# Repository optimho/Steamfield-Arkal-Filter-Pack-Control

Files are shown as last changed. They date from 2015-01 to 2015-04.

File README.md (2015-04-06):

# Steamfield-Arkal-Filter-Pack-Control

This controller was needed to supervise a filter pack that is installed in a remote location.
The filter pack will monitor the differential pressure over a series of filter packs, if the pressure gets too high the filter pack will 
initiate a series of back flushes. 

The filter pack is deficient in that, if it keeps flushing we need the filter to alarm and to open a bypass valve.

The filter controller was designed to monitor differential pressure input from a pressure sensor.
The controller also monitors the filter flush commands.

The firmware monitors for a high diff and filter run commands and alarms and bypasses the filter if required.

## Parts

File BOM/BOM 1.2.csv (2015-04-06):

RefDes | Value | Type | Pattern | RS Number
D1 |  | DBLS202G | DBS
D20 |  | 1N4007 | ES1GL Diode
D21 |  | LED | SML-31 LED
D23 |  | LED | SML-31 LED
HDR4_2 | 4 | TE connector 4 | 4 Way TE Connector | 452-612
HDR4_3 | 4 | TE connector 4 | 4 Way TE Connector | 452-612
HDR4_4 | 4 | TE connector 4 | 4 Way TE Connector | 452-612
HDR4_5 | 4 | TE connector 4 | 4 Way TE Connector | 452-612
J1 |  | HDR-1x8 | HDR-1x8
J2 |  | 1x2 Socket | CR0805
J3 |  | HDR-1x4 | HDR-1x4
J5 |  | 1x2 Socket | CR0805
J6 |  | 1x2 Socket | CR0805
J14 |  | 1x2 Socket | CR0805
K2.1 |  | G2R2 | G2R2 | 365-0529
K2.2 |  | G2R2 | G2R2
OPTOcoupler1 |  | CNY17F | CNY17F PDIP | 671-2699
OPTOcoupler2 |  | CNY17F | CNY17F PDIP | 671-2699
OPTOcoupler3 |  | CNY17F | CNY17F PDIP | 671-2699
OPTOcoupler4 |  | CNY17F | CNY17F PDIP | 671-2699
Q3 |  | BC639 | BCY-3/D5.2 | 800-9585
R1 | 10K | RES_0805 | RES_0805 | 788-3972
R19 | 2.2 micro henry | IND_0805 | IND_0805
R22 | 1k | RES_0805 | RES_0805 | 223-0427
R24 | 1k | RES_0805 | RES_0805 | 740-8971
R25 | 1k | RES_0805 | RES_0805 | 740-8971
R26 | 4700 ohm | RES_0805 | RES_0805 | 740-9031
R27 | 4700 ohm | RES_0805 | RES_0805 | 740-9031
R28 | 1k ohm | RES_0805 | RES_0805 | 740-8971
R29 | 1k ohm | RES_0805 | RES_0805 | 740-8971
R30 | 10k ohm | RES_0805 | RES_0805 | 788-3972
R31 | 10k ohm | RES_0805 | RES_0805 | 788-3972
R32 | 4700 ohm | RES_0805 | RES_0805 | 740-9031
R33 | 1k ohm | RES_0805 | RES_0805 | 740-8971
R34 | 1k ohm | RES_0805 | RES_0805 | 740-8971
R35 | 1k ohm | RES_0805 | RES_0805 | 788-3972
R36 | 10k ohm | RES_0805 | RES_0805 | 788-3972
R37 | 10k ohm | RES_0805 | RES_0805 | 788-3972
R42 | 1k ohm | RES_0805 | RES_0805 | 740-8971
R43 | 1k ohm | RES_0805 | RES_0805 | 740-8971
R44 | 1k ohm | RES_0805 | RES_0805 | 740-8971
R45 | 1k ohm | RES_0805 | RES_0805 | 740-8971
R48 | 2.0k | RES_2512 | RES_2512
R55 | 1k | RES_0805 | RES_0805 | 740-8971
R60 | 1K | RES_0805 | RES_0805 | 788-3972
R69 | 1k | RES_0805 | RES_0805 | 740-8971
R70 | 1K | RES_0805 | RES_0805 | 740-3971

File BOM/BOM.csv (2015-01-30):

RefDes | Value | Type | Pattern | RS Number | RS Number | Parallax_PN
C1 | 10 uF | CAP_1210 | T491 series size C |  |  | 210-10001
C3 | 10 uF | CAP_1210 | T491 series size C |  |  | 210-10001
C4 | 10 uF | CAP_1210 | T491 series size C |  |  | 210-10001
C5 | 1 uF | CAP_1210 | T491 series size A |  |  | 210-10001
C17 | 10 u farad | CAP | Aluminium Cap 8 x 6.2 | 490-8267 | 490-8267
C18 | 10 uf | CAP100RP | Aluminium Cap 8 x 6.2
C23 | 10u farad | CAP | T491 series size D
C24 | 3.3 u farad | CAP | Aluminium Cap 8 x 6.2
C25 | 3.3 uf | CAP_1206 | Aluminium Cap 8 x 6.2
D15 |  | 1N4002 | ES1GL Diode
D16 |  | DIODE_1206 | ES1GL Diode | 796-5800P | 796-5800P
D17 |  | DIODE_1206 | ES1GL Diode | 796-5800P | 796-5800P
D18 |  | DIODE_1206 | ES1GL Diode | 796-5800P | 796-5800P
D19 |  | DIODE_1206 | ES1GL Diode | 796-5800P | 796-5800P
D20 |  | 1N4007 | ES1GL Diode
D21 |  | LED | SML-31 LED
D22 |  | LED | SML-31 LED
D23 |  | LED | SML-31 LED
HDR4_1 | 4 | Header 4 | HDR-1X4 | 452-612 | 452-612
HDR4_2 | 4 | TE connector 4 | 4 Way TE Connector | 452-612 | 452-612
HDR4_3 | 4 | TE connector 4 | 4 Way TE Connector | 452-612 | 452-612
HDR4_4 | 4 | TE connector 4 | 4 Way TE Connector | 452-612 | 452-612
HDR4_5 | 4 | TE connector 4 | 4 Way TE Connector | 452-612 | 452-612
J1 |  | 1x2 Socket | CR0805 |  |  | n/a
J2 |  | 1x2 Socket | CR0805 |  |  | n/a
J12 |  | 1x2 Socket | CR0805 |  |  | n/a
J14 |  | 1x2 Socket | CR0805 |  |  | n/a
K1 |  | SWITCH8DIP | Dip Switch
K2.1 |  | G2R2 | G2R2 | 365-0529 | 365-0529
K2.2 |  | G2R2 | G2R2
OPTOcoupler1 |  | CNY17F | CNY17F PDIP | 671-2699 | 671-2699
OPTOcoupler2 |  | CNY17F | CNY17F PDIP | 671-2699 | 671-2699
OPTOcoupler3 |  | CNY17F | CNY17F PDIP | 671-2699 | 671-2699
OPTOcoupler4 |  | CNY17F | CNY17F PDIP | 671-2699 | 671-2699
Q3 |  | BC639 | BCY-3/D5.2 | 800-9585 | 800-9585
R1 |  | RES_0805 | RES_0805 | 788-3972 | 788-3972
R2 |  | RES_0805 | RES_0805 | 788-3972 | 788-3972
R19 | 2.2 micro henry | IND_0805 | IND_0805
R21 | 1K | RES_0805 | RES_0805 | 788-3972 | 788-3972
R22 | 1k | RES_0805 | RES_0805 | 223-0427 | 223-0427
R24 | 1k | RES_0805 | RES_0805 | 740-8971 | 740-8971
R25 | 1k | RES_0805 | RES_0805 | 740-8971 | 740-8971
R26 | 4700 ohm | RES_0805 | RES_0805 | 740-9031 | 740-9031
R27 | 4700 ohm | RES_0805 | RES_0805 | 740-9031 | 740-9031
R28 | 1k ohm | RES_0805 | RES_0805 | 740-8971 | 740-8971
R29 | 1k ohm | RES_0805 | RES_0805 | 740-8971 | 740-8971
R30 | 10k ohm | RES_0805 | RES_0805 | 788-3972 | 788-3972
R31 | 10k ohm | RES_0805 | RES_0805 | 788-3972 | 788-3972
R32 | 4700 ohm | RES_0805 | RES_0805 | 740-9031 | 740-9031
R33 | 1k ohm | RES_0805 | RES_0805 | 740-8971 | 740-8971
R34 | 1k ohm | RES_0805 | RES_0805 | 740-8971 | 740-8971
R35 | 1k ohm | RES_0805 | RES_0805 | 788-3972 | 788-3972
R36 | 10k ohm | RES_0805 | RES_0805 | 788-3972 | 788-3972
R37 | 10k ohm | RES_0805 | RES_0805 | 788-3972 | 788-3972
R38 | 10k ohm | RES_0805 | RES_0805 | 788-3972 | 788-3972
R42 | 1k ohm | RES_0805 | RES_0805 | 740-8971 | 740-8971
R43 | 1k ohm | RES_0805 | RES_0805 | 740-8971 | 740-8971
R44 | 1k ohm | RES_0805 | RES_0805 | 740-8971 | 740-8971
R45 | 1k ohm | RES_0805 | RES_0805 | 740-8971 | 740-8971
R46 | 220 ohm | RES_0805 | SMA | 721-6889P | 721-6889P
R47 | 666 ohm | RES_0805 | RES_0805 | 708-6070 | 708-6070
R48 | 2.0k | RES_2512 | RES_2512
R49 | 1k | RES_0805 | RES_1206 | 740-3971 | 740-3971
R50 | 1K | RES_0805 | RES_1206 | 740-3971 | 740-3971
R51 | 1K | RES_0805 | RES_1206 | 740-3971 | 740-3971
R52 | 1K | RES_0805 | RES_1206 | 740-3971 | 740-3971
R53 | 1K | RES_0805 | RES_1206 | 740-3971 | 740-3971
R54 | 1K | RES_0805 | RES_0805 | 740-8971 | 740-8971
R55 | 1k | RES_0805 | RES_0805 | 740-8971 | 740-8971
R56 | 1K | RES_0805 | RES_1206 | 740-3971 | 740-3971
R57 | 1K | RES_0805 | RES_1206 | 740-3971 | 740-3971
R58 | 1K | RES_0805 | RES_1206 | 740-3971 | 740-3971
R59 | 10K | RES_0805 | RES_0805 | 788-3972 | 788-3972
R60 | 1K | RES_0805 | RES_0805 | 788-3972 | 788-3972
R61 | 10K | RES_0805 | RES_0805 | 788-3972 | 788-3972
R62 | 10K | RES_0805 | RES_0805 | 788-3972 | 788-3972
R63 | 10K | RES_0805 | RES_0805 | 788-3972 | 788-3972
R64 | 10K | RES_0805 | RES_0805 | 788-3972 | 788-3972
R65 | 10K | RES_0805 | RES_0805 | 788-3972 | 788-3972
R66 | 10K | RES_0805 | RES_0805 | 788-3972 | 788-3972
R67 | 10K | RES_0805 | RES_0805 | 788-3972 | 788-3972
R69 | 1k | RES_0805 | RES_0805 | 740-8971 | 740-8971
R70 | 1K | RES_0805 | RES_0805 | 740-3971 | 740-3971
S1 |  | Pushbutton | Tactile Switch | 793-1642 | 793-1642 | 400-10003
U1 |  | P8X32A-Q44 | LQFP_44/10x10x0.8 | 450-626p | 450-626p
U2 |  | 24LC256MS | TSOP-8/3x6 | 738-0069 | 738-0069
U3 |  | LM1086IS-3.3 | TO263-4/14x10.2x2.54 | 533-9426P | 533-9426P
U9 |  | LM338T | SFM-3/W10.7 | 640-7839 | 640-7839
X1 |  | CRYSTALHC49U-V | HC49U-V | 814-9396P | 814-9396P

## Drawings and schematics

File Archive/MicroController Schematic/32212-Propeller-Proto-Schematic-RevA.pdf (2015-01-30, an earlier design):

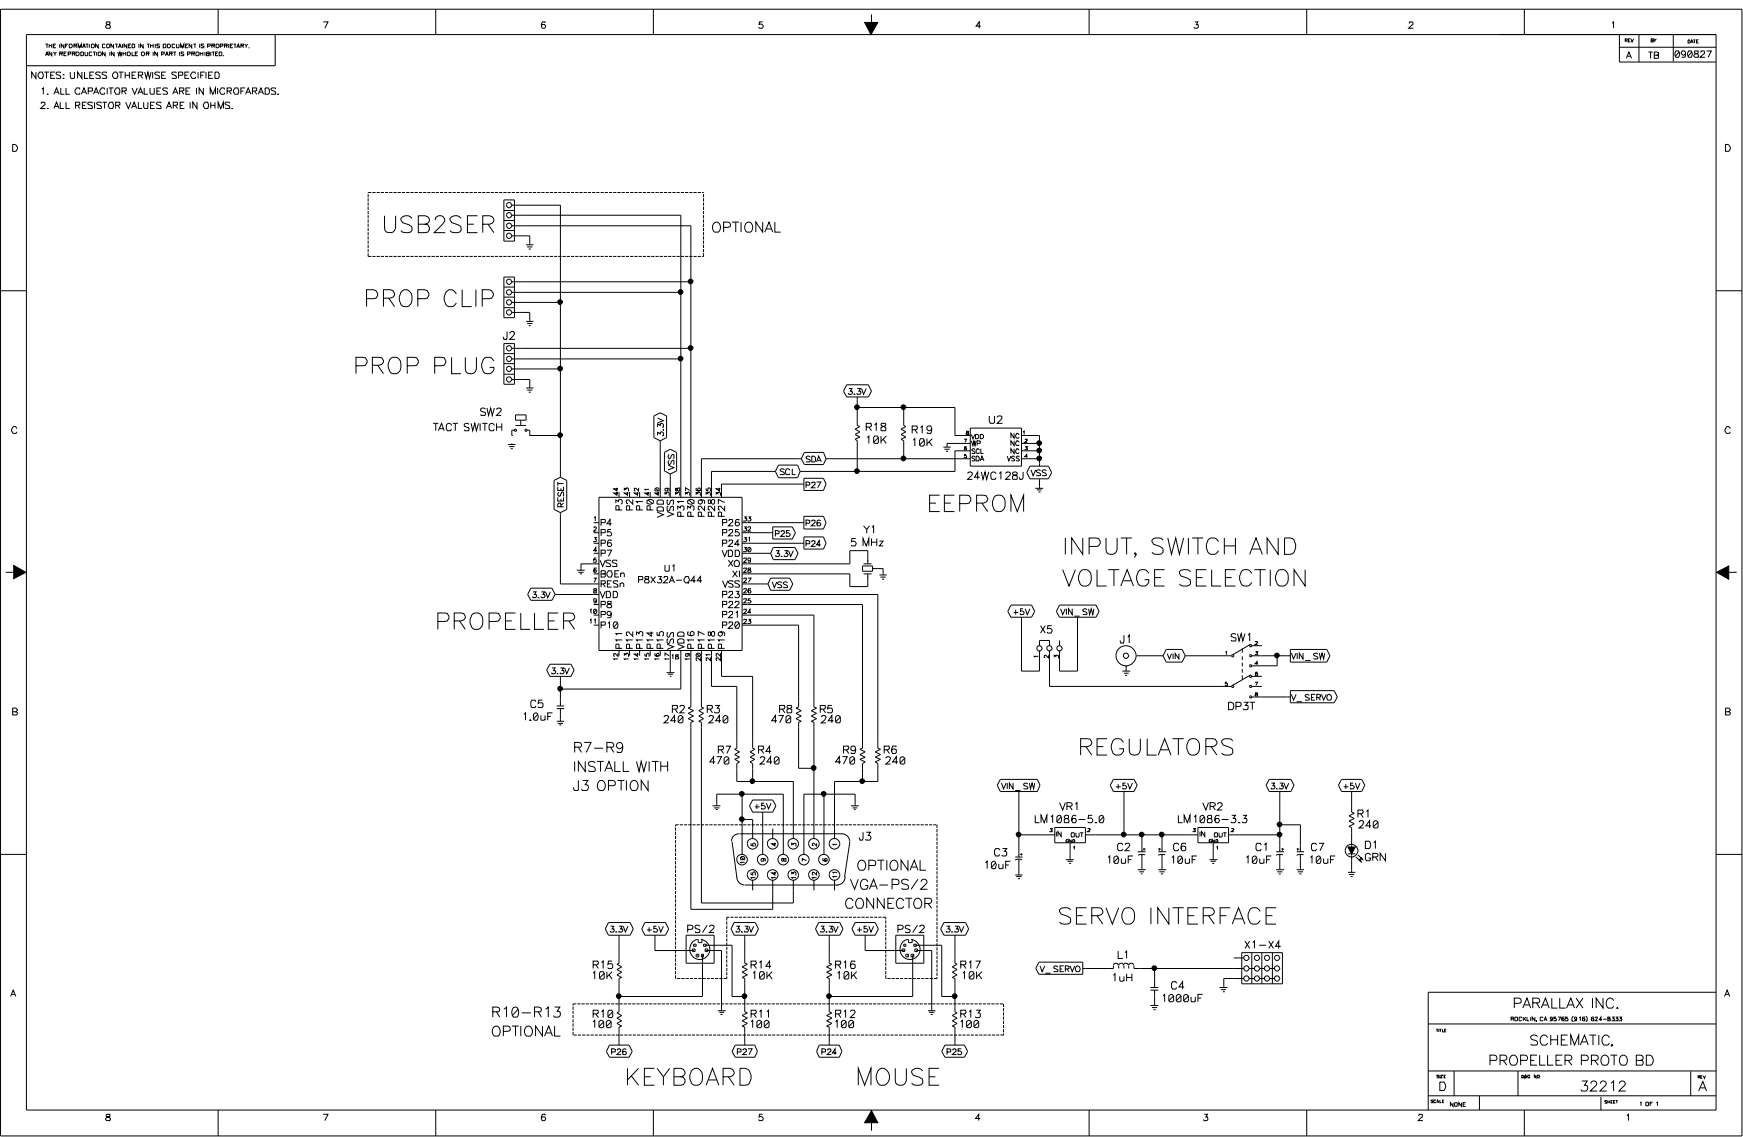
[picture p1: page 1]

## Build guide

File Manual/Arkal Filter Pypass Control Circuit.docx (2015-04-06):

Arkal Filter Control

Contact Energy

Filter Control Board

https://github.com/optimho/Steamfield-Arkal-Filter-Pack-Control

###### Table of Contents

###### Operation

t

He Filter control module monitors the differential pressure across the filter Pack and also counts the amount of filter flush cycles. If the filter pack is constantly flushing and not able to clear the high differential, then the bypass will be opened and an alarm will be raised.

Refer to the Arkal filter documentation to maintain a blockage in the filter.

All documentation for the project is available on Github, follow the following URL

https://github.com/optimho/Steamfield-Arkal-Filter-Pack-Control

###### Control

The reset button will be illuminated on the front of the panel if the filter control has operated the bypass valve. To resume normal operation reset the filter control by pressing the illuminated button. The light should extinguish and the bypass valve should close, if the DP (Differential Pressure) has returned to normal.

###### Settings

The board was originally designed with dipswitches, but the dipswitch was resigned and the firmware was added to the project. All changes and customization can be done directly in the firmware.

If you want to modify or monitor the controller install the Simple IDE software that is available at the Github address above under the firmware folder.

# Connection Diagram

###### Maintenance

There is no maintenance required apart from testing and inspecting the operation of the controller at regular intervals.

###### Schematics

###### Firmware Listing

/*

*

*SteamFileldController.c

*

*Main listing

Steamfield Controller Firmware

controls the bypass valve, opens if the flush cycles are to numerous.

functions recordEvent( period) this function will return the amount of operations preformed in a specified period in seconds

The function is a low speed function and cannot really handle inputs at a frequency less than 1 second.

*/

#include <TimeFile.h>

#define period 90 // This is the period that the amount of flush starts are counted

#define diffAlarm 10 // This is the period that initiates a diff Alarm

#define flushValve 26 //

#define highDiff 1 //

#define filter1 2 //define the micro processor pin usage

#define filter2 3 //

#define filter3 4 //

#define clear 5 // Reset input

#define FilterStarts 5

char *timeOfEvent;

int i=0;

int placeHolder1=0;

int placeHolder2=0;

int placeHolder3=0;

int diffState=0; // Time differential pressure became high

int diffTime=0;

int currentTime=0; // The amount of seconds since the last time reset or switch on

int amountOfEvents=0; // amount of flush operations recorded in a specified period

int main()

{

print("********************************* \n");

print("********************************* \n");

print("******* Steamfield *****\n");

print("**** Arkal filter controller ***\n");

print("**** Contact Energy **** \n");

print("********************************* \n");

print("****** Michael *** \n");

print("****** Rick *** \n");

print("****** Grant *** \n");

print("********************************* \n");

print("**** 15-03-2015 version 1.0 ** \n");

print("********************************* \n");

print(" \n");

print(" \n");

pause(1000);

for(;;)

{

int diff = input(highDiff);

int flush_1 = input(filter1);

int flush_1_old;

int flush_2 = input(filter2);

int flush_2_old;

int flush_3 = input(filter3);

int flush_3_old;

int clr = input(clear);

currentTime=timeNow(); // the time now is currentTime

/* This section is to determine if a flush cycle has been completed.

* ************************************************************************/

if (placeHolder2 != sequenceCheck(flush_1, flush_2, flush_3))

{

//print(" Flush sequence complete %d \n", sequenceCheck(flush_1, flush_2, flush_3));

}

placeHolder2=sequenceCheck(flush_1, flush_2, flush_3);

/* Prints to terminal some program information

* ************************************************************************/

if (placeHolder1 != indexer())

{

print("number of filter starts %d per %d seconds - filter %d %d %d \n", indexer(), period, flush_1, flush_2 ,flush_3);

}

placeHolder1=indexer();

//printf("amount of triggers per period %i \n", amountOfEvents);

// printf("Seconds since last reset %i \n",currentTime);

// print("diff Pressure = %d\n", diff);

// print("flush 1 = %d\n", flush_1);

// print("flush 2 = %d\n", flush_2);

// print("flush 3 = %d\n", flush_3);

// print("Diff High since = %d \n", diffState);

// print("************************ \n");

//print(" \n");

/* This section is to determine if a flush has been initiated.

* ************************************************************************/

if ((flush_1 > flush_1_old) || (flush_2 > flush_2_old) || (flush_3 > flush_3_old))

{

amountOfEvents=recordEvent();

}

flush_1_old=flush_1;

flush_2_old=flush_2;

flush_3_old=flush_3;

/* This section is to determine how long the high diff alarm has been active.

* ************************************************************************/

if ((diff==1) && (diffState==0)) //If there is a high diff and there is not currently a high diff already then save the time

{

diffState = currentTime;

//diffTime = diffState; // That the diff went high

}

else if ((diff==1) && (diffState>0)) //If there is a high diff and there is not currently a high diff already then save the time

{

diffTime = currentTime-diffState; // That the diff went high

}

else if ((diff==0)&& (diffState>0) ) // If the diff clears and the diff was high consider that the high diff to have cleared.

{

diffTime = 0;

diffState = 0;

//

}

/* This program segment alarms if the filter starts per time period is exceeded. */

if (placeHolder1>FilterStarts)

{

high(flushValve);

}

/* This code segment is the Reset part that resets all counters

* **************************************************************

* **************************************************************/

if (clr==1)

{

clrEvents();

low(flushValve);

}

/********************************************************************

****************************************************************/

/* Print to terminal if DIFF pressure is high.

* ************************************************************************/

if ((diffTime > diffAlarm))

{

print("diff Alarm %d \n",currentTime );

pause(1000);

}

placeHolder3=diff;

/* This section of the code is to zero the clock periodially so that you do not get any math mathmatical errors if the clock rolls over to zero.

/* This decison to zero the clock is only made when all variables are in the zero state past some time in the future .

* Diff pressure is reset and there has been no flush cycles in the last period and the time is > than 1000000 seconds

* *********************************************************************************************************************************************/

if ((diff==0) && (diffState==0) && (currentTime>1000000) && (amountOfEvents==0))

{

settime();

}

/* This code must be called regularly to make sure that only the events within the specified period are recorded -- this filter also put

* a reasonable processor overhead so it is good to call it once per main loop period so that each loop iterates at the same speed.

**********************************************************************************************************************************************/

reducer(period); //in a period

}

return 0;

}

*/

TimeFile.c

*/

#include <TimeFile.h>

#define BUFFERLEN 10

//time_t now;

int timeNow(void)

{

// time_t now;

now = time(NULL);

// printf("%s", asctime(localtime(&now)));

// printf("%i \n", now);

return now;

}

void printtime(void)

{

now = time(NULL);

printf("%i", &now);

return asctime(localtime(&now));

}

int getdst(void)

{

int rc = 0;

printf("Use daylight savings time [y/n] ?");

fflush(stdout);

rc = (getchar() == 'y') ? 1 : 0;

getchar();

return rc;

}

int prompttime(char *prompt)

{

int rc = 0;

char *endp;

char buffer[BUFFERLEN];

do {

printf("Enter %s: ",prompt);

fflush(stdout);

fgets(buffer,BUFFERLEN,stdin);

fflush(stdin);

rc = strtol(buffer, &endp, 10);

if(endp == buffer)

{

if('\n' == *endp)

{

rc = 0;

break;

}

printf("Invalid entry \"%c....\" Please enter a number.\n", *endp);

}

} while(endp == buffer);

return rc;

}

void settime(void) // set time virtual RTC

{

struct timeval tv;

struct tm t;

t.tm_isdst = 0; //getdst();

t.tm_year = 1968-1900; //prompttime("Year")-1900;

t.tm_mon = 11-1; //prompttime("Month")-1;

t.tm_mday = 11; //prompttime("Day of the month");

t.tm_hour = 12; //prompttime("Hour");

t.tm_min = 0; //prompttime("Minute");

t.tm_sec = 0; //prompttime("Second");

tv.tv_sec = mktime(&t);

settimeofday(&tv, 0);

// printf("Set time all done.\n");

}

int recordEvent()

{

int a=indexer();

currentEventTime[a]=timeNow();

return indexer();

}

/* How many items in the array, count any non zero entries*/

int indexer()

{

int i=0;

while (currentEventTime[i]!=0)

{

i++;

}

return i;

}

/*Filter through the EventTime array and remove events that are older than a value in seconds */

void reducer(period)

{

int interval=period;

int currentTime = timeNow();

int Events=100;

int i=0;

while (currentEventTime[i]!=0)

{

i++;

}

i=0;

if ((currentTime-interval>currentEventTime[0]) && (currentEventTime[0]>0))

{

shiftArray(indexer());

}

}

shiftArray(int numberOfElements)

{

for (int i=1; i<=numberOfElements; i++)

{

currentEventTime[i-1]=currentEventTime[i];

}

}

int sequenceCheck(flush1, flush2, flush3)

{

if ((flush1==1) && (gv_sequence==0))

{

gv_sequence=1;

return gv_sequence;

}

else if ((flush2==1) && (gv_sequence==1))

{

gv_sequence=2;

return gv_sequence;

}

else if ((flush3==1) && (gv_sequence==2))

{

gv_sequence=3;

return gv_sequence;

}

else

{

gv_sequence=0;

return gv_sequence;

}

}

/* ********************void clear records **************************************/

void clrEvents()

{

int i=0;

while (currentEventTime[i]!=0)

{

currentEventTime[i]=0;

i++;

}

}

/*

* Header File

*

* TimeFile.h

*

*

*/

#include <time.h>

#include <sys/time.h>

#include <simpletools.h>

#define TRUE 1

#define FALSE 0

#define FAIL 0

time_t now;

int gv_sequence; // Global variable for the sequence function

volatile int currentEventTime[1000];

int *addr;

int timeNow(void); /* The time now is the time since the epoch which is 1 January 00:00:00 1970 */

void shiftArray(int numberOfElements); /* Rapidly shift all the elements of an array by one/*/

volatile struct timeStruct{

int hour;

int min;

int sec;

}EventTime[10];

void printtime(void);

int getdst(void);

int prompttime(char *prompt);

void settime(void);

void starts_per_hour( int i);

int recordEvent(); /* inserts a time event onto an array and returns an integer of the amount of events per

period in seconds */

int indexer(); /* counts how many entries are in the array */

void reducer(int period); /* keeps all entries current within the last period period is in seconds */

int totSec(int i); /* calculates the total amount of seconds in EventTime[x] */

int sequenceCheck(int flush1,int flush2,int flush3); /* Returns True if a flush cycle is complete, that means that

Filter1 then filter 2 then after that filter 3 */

void clrEvents(); /* Clears all records back to zero .*/

Filter Control

Design Customization

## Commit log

2015-01-30 All the Arkal filter files
    [BOM.csv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]
2015-04-06 Modifications to version 1.1b
    Version 1.1b had a few complications. version 1.2 is a daughter board
    that fits onto the Parallax project board.
    [BOM 1.2.csv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]
2015-04-06 Added Parallax Project Board schematics
    The Parallax project is a low cost board that I have used to build the
    filter. We have a good stock of factory rejects that have a minor error
    on.
    [BottomAssy.gbr]
2015-04-06 Simple IDE
    Simple IDE is the software used to maintain the Filter control board
2015-04-06 Deleted old gerber files
    [Board.gbr, BoardOutline.gbr, Bottom.gbr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]
